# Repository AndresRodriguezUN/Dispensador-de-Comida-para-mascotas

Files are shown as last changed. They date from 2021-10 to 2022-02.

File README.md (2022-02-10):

# Dispensador de Comida para mascotas 🐱 🐶
## Autores :fountain_pen:
- Diego Steven Peña Cortes :mechanic:
- Daniel Machado Roa :technologist:
- Andrés Felipe Rodríguez Contreras :office_worker:  :shipit:

Este es el repositorio del proyecto final de la asignatura Sistemas Emebidos del semestre 2021-II (Universidad Nacional de Colombia - Sede Bogotá). A continuación se mostrará el proyecto de un Dispensador de Comida conformado por una arquitectura de SoC, donde a partir de un micropocesador y diferentes periféricos se realizan operaciones que permiten al dispensador vincularse con un dispositivo movil para configurar la alimentación de la mascota.
 
 ## Proyecto :open_file_folder:
 El proyecto consiste en un dispensador de comida para mascotas que dispone de funcionalidades como la comunicación con una app movil que permite la configuración del dispositivo y el funcionamiento del mismo. Dentro del funcionamiento se encuentra la programación de los horarios de alimentación, asi como la interacción entre el usuario-dispositivo-mascota.
 
Por otro lado, el dispositivo cuenta con sensores que permiten detectar si la mascota está comiendo, además de los horarios que frecuenta el dispositivo. Y de esta manera, puede realizar un análisis de los datos y retroalimentar al usuario por medio de la actualización de los comportamientos de su mascota frente al dispositivo. Permitiendo que no se pierda la conexión que tiene el usuario con su mascota.  
 
 ## [Motivación](/Motivacion/) :thought_balloon:
 
 Con el fin de de justificar el proyecto, se definieron los viajes tanto del cliente como de la mascota y del como intervenía nuestro proyecto en cada uno de los trayectos. Esto permitio resaltar las funcionalidades directas o indirectas que debe cumplir el dispositivo a desarrollar. De esta forma se definieron los periféricos necesarios, además del módulo-procesador que se van a utilizar.

 ## Flujo de procesos
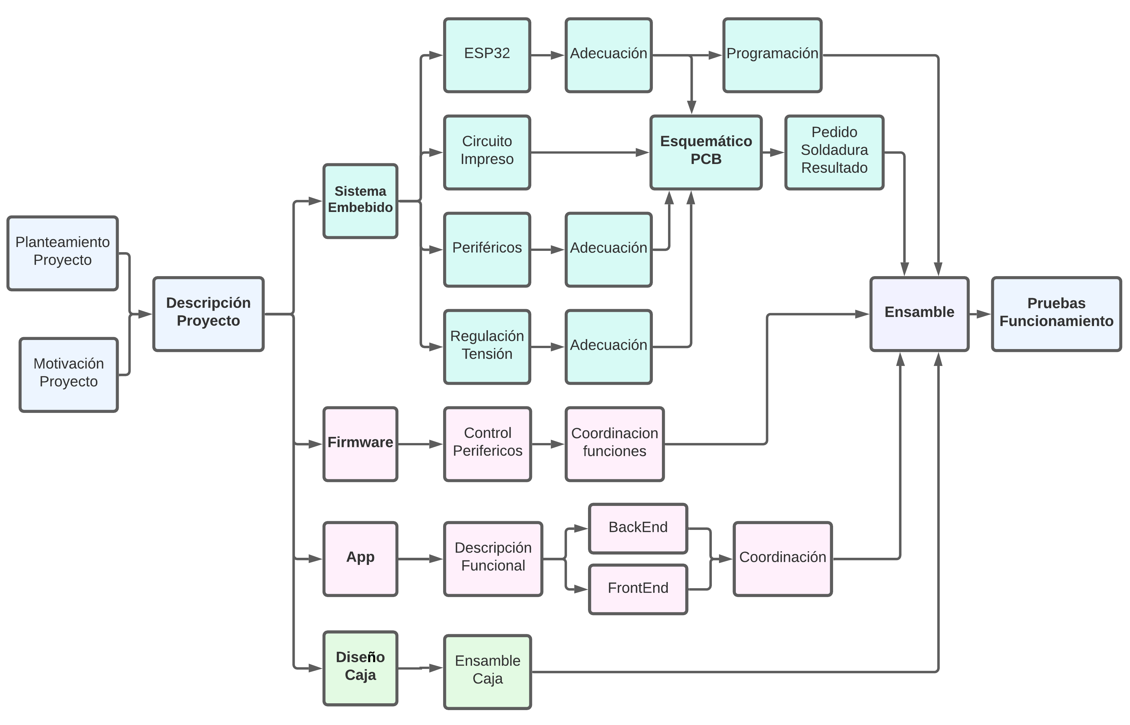
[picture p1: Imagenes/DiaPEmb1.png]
 

 ## [Sistema embebido](/SoC/)  :computer:
 
 El sistema embebido se definio gracias al análisis previo de las funcionalidades directas e indirectas del dispositivo, las cuales permitieron decidir los periféricos necesitados para cumplir cada una de las funcionalidades del proyecto.
 
### Periféricos

- [Pantalla OLED - I2C](/Perifericos/OLED)

- [Sensor de movimiento](/Perifericos/SensorMov)

- [Sensor infrarrojo](/Perifericos/SensorInfra)

- [Control motor - ULN2003](/Perifericos/Motor)

- [DFPlayer Mini](/Perifericos/DFPlayer)
 
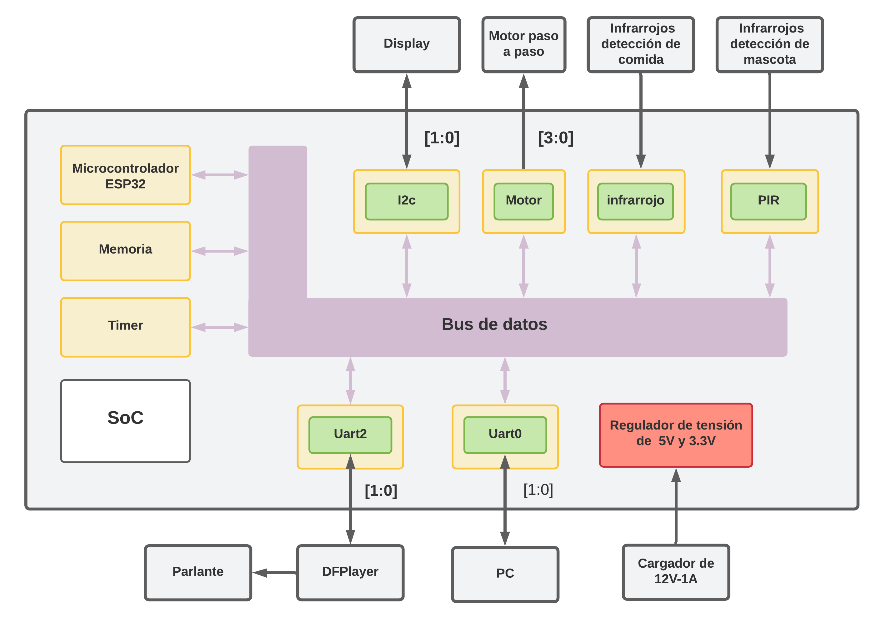
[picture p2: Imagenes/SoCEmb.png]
 
 
  ## Finalidad coordinación de periféricos :nut_and_bolt:
  
  La idea es construir un dispositvo que a determinadas horas del dia ponga a disposición una porcion de comida para nuestra mascota. Esta meta se cumple con las prestaciones que nos ofrece cada uno de los componentes a ensamblar:
  
  - Tarjeta basada en ESP32: Encargada de la coordinación de los périfericos y la comunicación inalámbrica con una App.
  - App: Encargada de la retroalimentación del usuario sobre el estado de la mascota, además de la posibilidad de programar los horarios de comida que el usuario desée para su mascota.
  - Motor: Encargado de la rotación del plato en el cual estan alojadas cada una de las porciones de comida.
  - OLED: Encargado de dar una retroalimentación visual, en el dispositivo, del estado de la mascota.
  - DFP y Parlante: Encargados de reproducir una pista de audio que avise a la mascota cuando llegue la hora de comer.
  - PIR: Encargado de detectar si la mascota se acerca al dispositivo dispensador de comida, para evaluar indirectamente su estado de ánimo.
  - Infrarrojo: Encargado de detectar si la mascota ha comido alguna parte de su ración, para evaluar indirectamente su estado de ánimo.
 
Al tener todo coordinado se espera que se cumpla la finalidad del proyecto satisfactoriamente.

## [Firmware](/Firmware) :man_technologist:
El firmware de todo el proyecto se desarrolla en micropython, el cual es una version renderizada de python para poder ejecutarse en microcontroladores como lo es el ESP32. Se decidio utilizar micropython debido a su practicidad y la documentación amplia que tiene en distintos repositorios. Con respecto al ESP32 cabe destacar que se debe flashear con micropython para que todos los códigos en python que se deseen emplear se ejecuten a la perfección. Para más información sobre el manejo de micropython junto al ESP32 por favor remitase a [micropython-esp32](https://docs.micropython.org/en/latest/esp32/tutorial/index.html).

## [App](/App) :calling:

Para poder manejar el dispensador de alimentos para mascotas se creó una aplicación, la cual permita modificar los valores de tiempo en que se servirán las comidas y a su vez saber el estado en que se encuentra la mascota.

## [Diseño Caja](/Rcaja) :triangular_ruler: :package:

Se diseñó un contenedor (carcasa o caja) la cual permitiera tener el dispensador dentro de una estructura con el fin de almacenar el plato con la comida y el sistema embebido, por lo tanto, se tomaron las diferentes medidas de los periféricos para poder crear los planos en *CorelDraw* y crear la carcasa en madera gracias al proceso de corte láser.

## [Ensamble](/Ensamble) :wrench:

En esta sección se muestra el paso a paso de la unión del sistema embebido y el plato que contiene la comida con la carcasa por medio de imágenes que dan evidencia de este proceso. 

## Pruebas de funcionamiento y videos de referencia :clapper:

### Videos de referencia
Para encontrar los videos que se recomiendan a lo largo del repositorio por favor dirijase a [videos proyectos pasados](https://www.youtube.com/channel/UCFcKXg10MjH98TOnZhloZSA).

### Pruebas de funcionamiento

Se realizaron las siguientes pruebas de funcionamiento del dispositivo y la App.

- [Prueba 1](https://youtu.be/kQyHtM4AsF8).
- [Prueba 2](https://youtu.be/hgBiyUTOZwg).

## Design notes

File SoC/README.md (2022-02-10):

# Sistema embebido :computer:

## [Microcontrolador ESP32](/SoC/ESP32/)
Se implementó un microcontrolador ESP32-WROOM, el cual se encargara de coordinar los diferentes periféricos a implementar. Igualmente, gracias a su periférico de WiFi se podrán utilizar las comunicaciones inalámbricas en lo que respecta a la conexión con la App de control.

- [Adecuación y acondicionamiento](/SoC/ESP32#adecuaci%C3%B3n)
- [Programación](/SoC/ESP32#programaci%C3%B3n)

## Periféricos

En base al sistema embebido definido previamente, se llegó a la conclusión que los periféricos necesarios para cumplir con las funcionalidades directas del dispositivo son:

- [Pantalla OLED - I2C](/Perifericos/OLED)

- [Sensor de movimiento](/Perifericos/SensorMov)

- [Sensor infrarrojo](/Perifericos/SensorInfra)

- [Control motor - ULN2003](/Perifericos/Motor)

- [DFPlayer Mini](/Perifericos/DFPlayer)

## [Regulación de tensión](/Regulador)

Dado que en proyecto se utiliza un ESP32-WROOM, este necesita una tensión de 3.3V para funcionar y por otro lado se necesitan 5V para poner en funcionamiento un motor paso a paso que se encargara de las prestaciones mecanicas del dispositivo. Por lo tanto se implementan dos reguladores de tension en la tarjeta que se desarrolle.

## [Circuito Impreso](/SoC/CircuitoImpreso)

Para el proyecto se decidio implementar un circuito impreso, el cual debera contar con el microcontrolador y los diferentes acondicionamientos necesarios para el manejo y control de los distintos periféricos a emplear.

- [Esquematico](/SoC/CircuitoImpreso#esquematico---kicad)
- [Asignacion de Footprints](/SoC/CircuitoImpreso#asignaci%C3%B3n-de-footprints)
- [PCB](https://github.com/AndresRodriguezUN/Dispensador-de-Comida-para-mascotas/tree/main/SoC/CircuitoImpreso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)
- [Pedido](/SoC/CircuitoImpreso#pedido---fabricante-chino)

## [Soldadura y Resultado](/SoC/Soldadura)

Con el circuito impreso entregado por el fabricante, se procede a realizar la soldadura de cada uno de los componentes comprados para el dispositivo dispensador de comida para mascotas.

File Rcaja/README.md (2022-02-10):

## Diseño de Caja :triangular_ruler::package:

Para realizar el diseño de la caja primero se debieron tener en cuenta el plato en donde se servirá la comida a la mascota, para esto se consiguió un plato de 21cm de diámetro con 8 cm de alto. A su vez, se deben tener en cuenta que para su creación se usó corte laser en madera, por lo tanto no se podría realizar una forma redonda a la carcasa, de esta manera se optó por formar un octágono que encierre el diámetro del plato sin problemas.

También cabe destacar que se debieron tener en cuenta los espacios de los periféricos dentro de la carcasa, como por ejemplo el motor, dando así que se agregaran 3 cm de alto a la carcasa (11cm). Así mismo,están diferentes periféricos que se les debe crear un espacio en las paredes de la carcasa para la interacción externa con estos, los objetos y sus medidas en la caja se presentan a continuación:

- OLED: 2.5cm x 1.5 cm
- Interuptor: 1.9cm x 1.2cm
- Conección alimentación: 9cm x 11cm
- Sensor PIR: 9mm diametro
- Conección USB: 1.5cm x 0.6 cm

Por lo tanto, teniendo en cuenta lo anterior se decidió realizar el proyecto el el programa de *CorelDraw* dando asi los siguientes planos:

<p align="center">
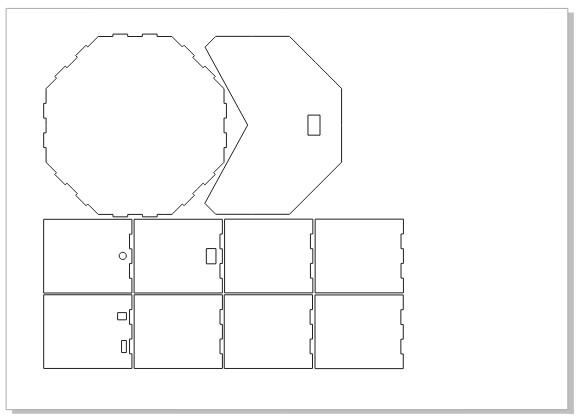
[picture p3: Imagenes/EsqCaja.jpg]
  

Por último, luego de mandar a cortar una tabla de madera en corte laser se obtuvo el siguiente resultado:

<p align="center">
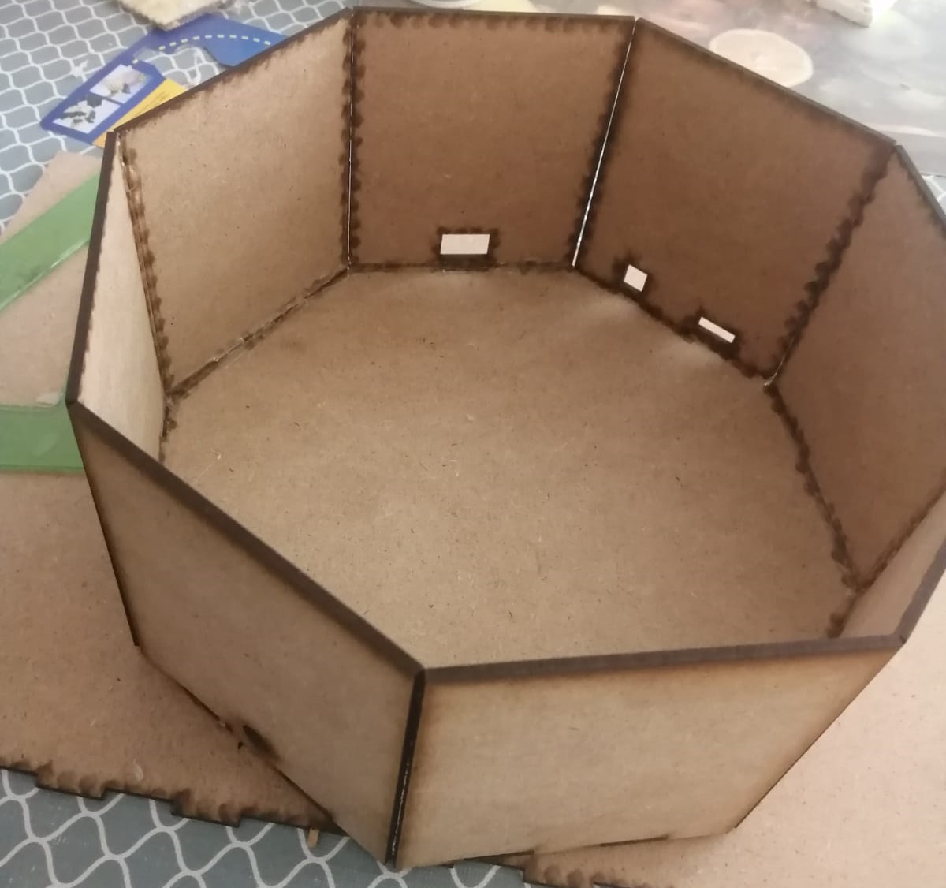
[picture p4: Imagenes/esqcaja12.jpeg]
  
</p>
<p align="center">
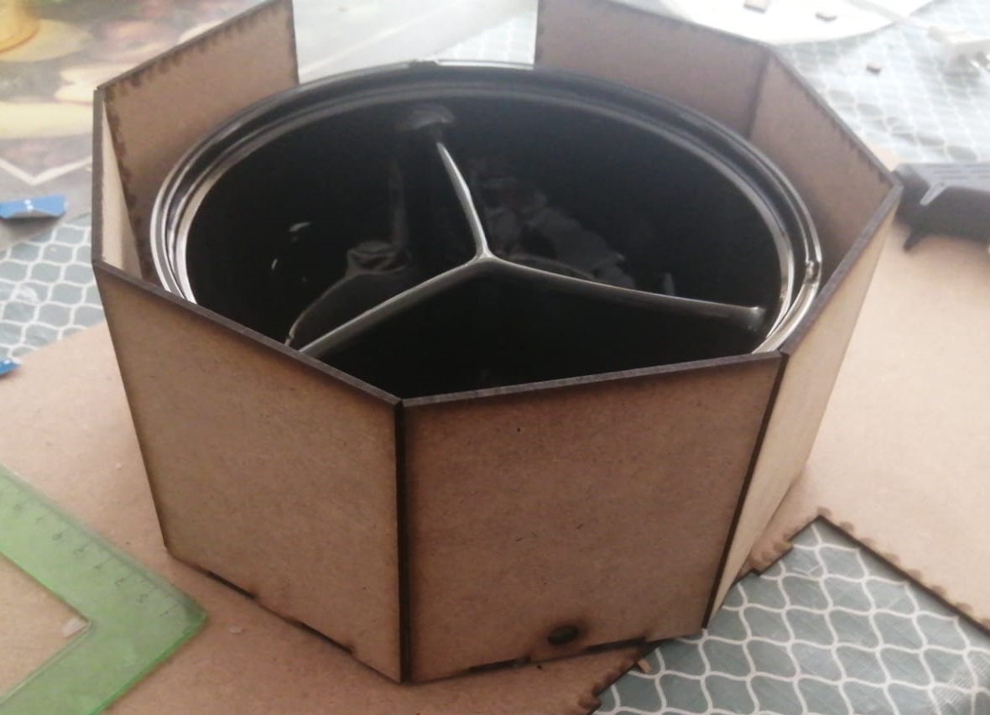
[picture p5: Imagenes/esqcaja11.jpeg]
  
</p>

Ya con la carcasa ensablada y las paredes pegadas, se puede pasar a colocar el circuito, los perifericos y el plato dentro para comenzar a hacer pruebas.

<p align="center">
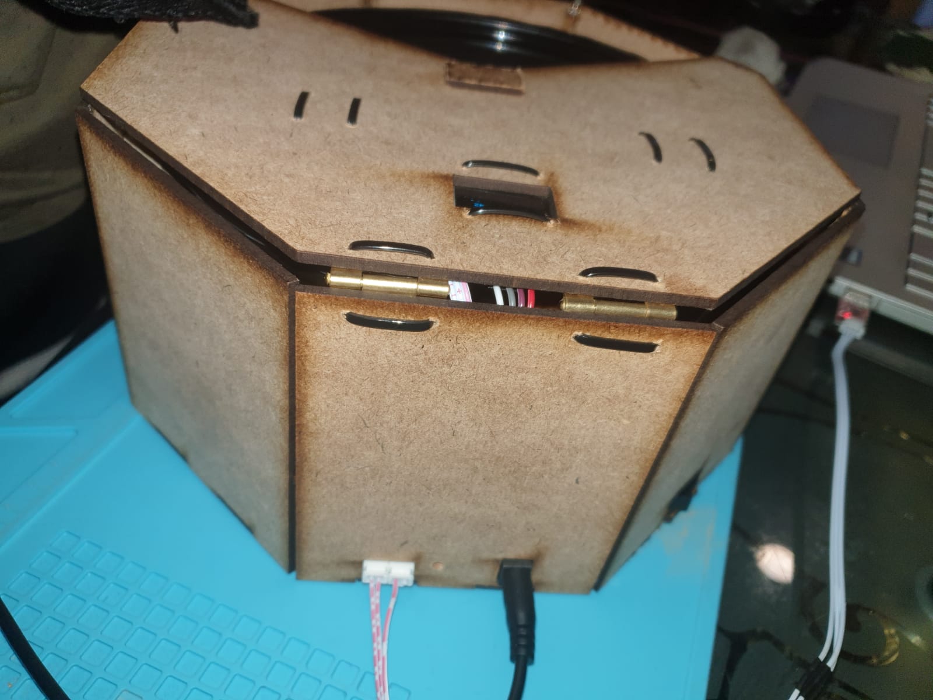
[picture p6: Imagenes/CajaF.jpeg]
  
</p>
<p align="center">
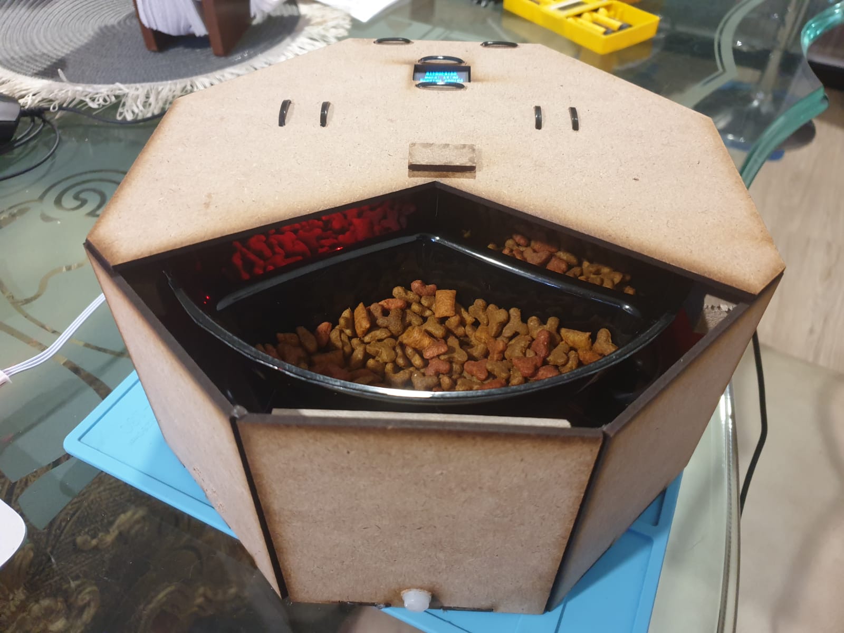
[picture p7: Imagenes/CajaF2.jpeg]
  
</p>

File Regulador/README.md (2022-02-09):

# Regulación de tension

El proyecto se utiliza un ESP32-WROOM, este necesita una tension de 3.3V para funcionar y por otro lado se necesitan 5V para poner en funcionamiento un motor paso a paso que se encargara de las prestaciones mecanicas del dispositivo. Por lo tanto se implementan dos reguladores de tension en la tarjeta que se desarrolle.
Con el fin de regular la tensión a 3.3 V y 5 V, se utilizan reguladores NCP1117-3.3 y NCP1117-5 con el empaquetado SOT-223.
<p align="center">
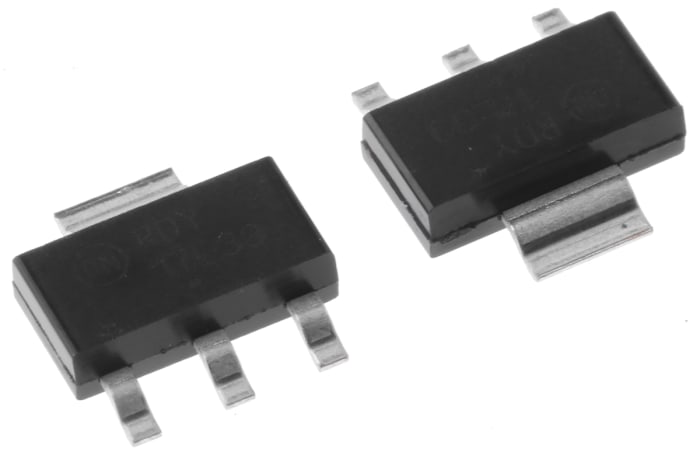
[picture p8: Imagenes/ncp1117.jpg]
  
</p>

## Diagrama de conexiones
Es importante identificar los pines de cada uno de los empaquetados para el correcto montaje sobre el circuito impreso, asi como el acondicionamiento que es necesario darles para su correcta implementacion.

<p align="center">
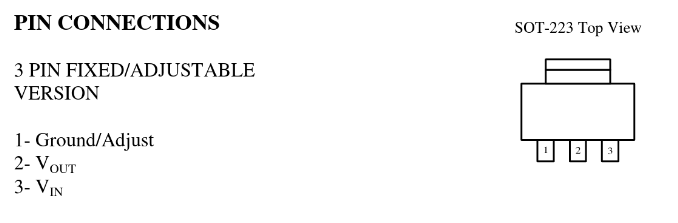
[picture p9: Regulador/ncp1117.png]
  
</p>

## Adecuacion
Segun el datasheet es necesario utilizar capacitores de 10uF y 47uF en la entrada y la salida correspondientemente, para cada una de las configuraciones de los reguladores de montaje SMD que se utilizaran en el circuito impreso. 

<p align="center">
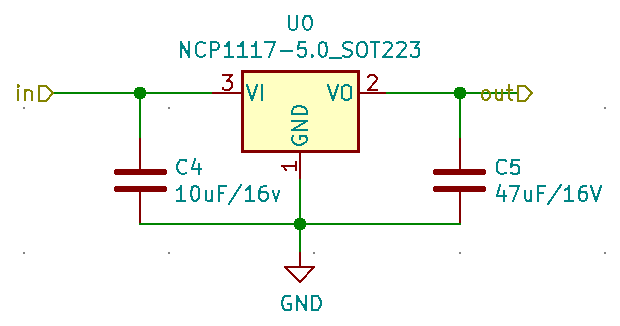
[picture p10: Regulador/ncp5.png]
  
</p>
<p align="center">
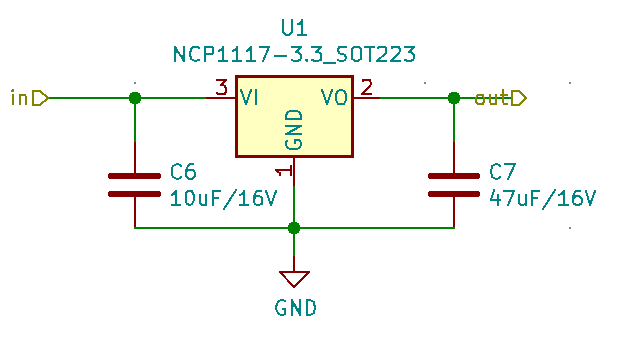
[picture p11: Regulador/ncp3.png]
  
</p>

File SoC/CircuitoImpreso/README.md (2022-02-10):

# Circuito Impreso
El circuito impreso se desarrolla teniendo en cuenta las adecuaciones y acondicionamientos que necesitan tanto el ESP32, los reguladores de tension y los perifericos. Para el desarrollo del esquematico y la PCB se utilizo el software de kiCAD, al cual fue necesario adicionarle las librerias correspondiente al esquematico del ESP32-WROOM y el footprint para la PCB.

## Esquematico - KiCAD
Despues de realizar el analisis de los distintos componentes y de los acondicionamientos necesarios, se realizo el esquematico en KiCAD de todo el proyecto. Incluyendo otras partes necesarias en hardware para la sujecion y conexion del sistema embebido. Igualmente dentro del repositorio se incluye el archivo del esquematico al cual puede remitirse para verificar todo lo diseñado [kiCAD](/kiCAD). 

### ESP32-WROOM
- Conexiones en general del microcontrolador.
<p align="center">
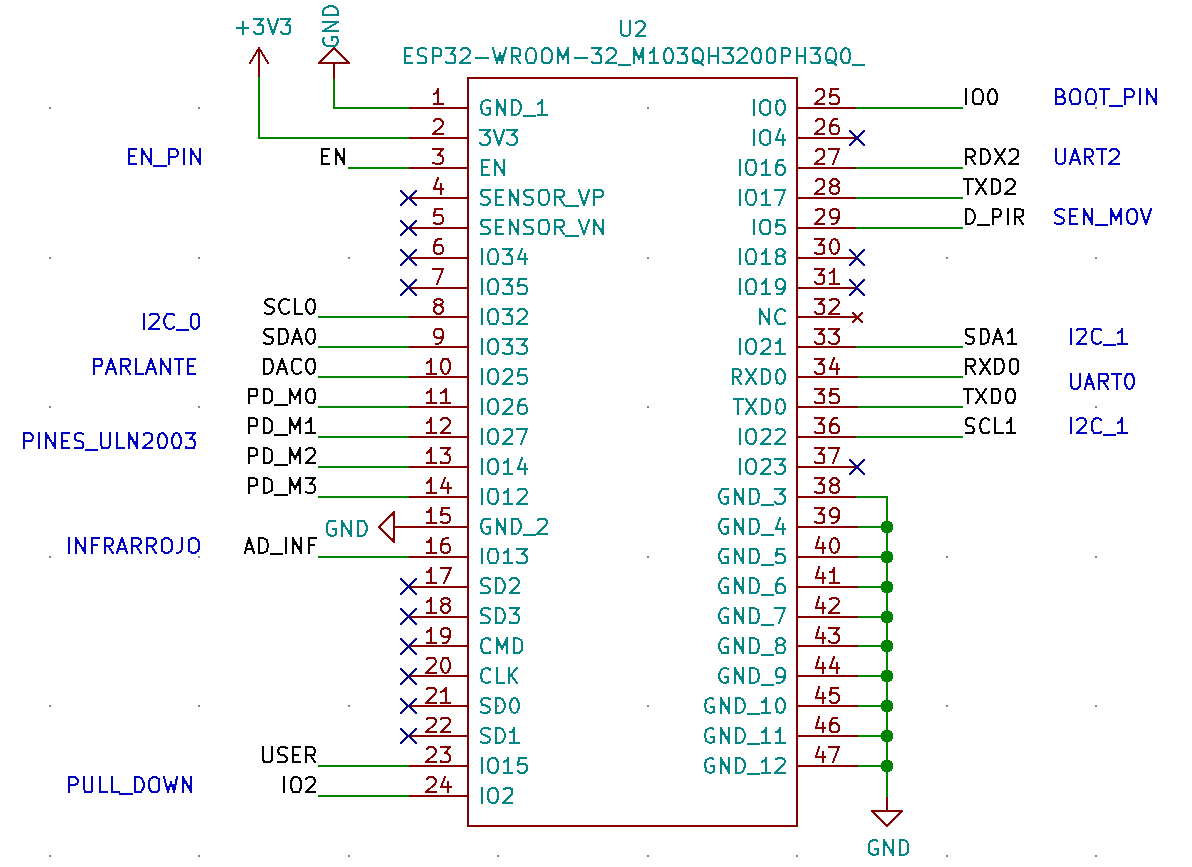
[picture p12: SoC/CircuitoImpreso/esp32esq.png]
  
</p>

- PIN USER: Este Pin se utiliza para interactuar visualmente con el ESP32 y verificar si funciona correctamente tanto la recepcion, como transmision de datos.

<p align="center">
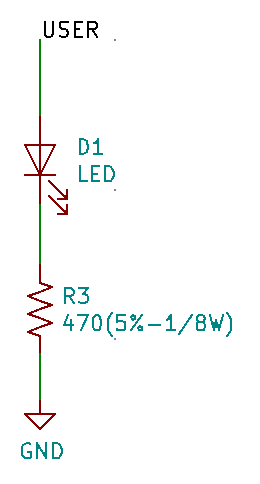
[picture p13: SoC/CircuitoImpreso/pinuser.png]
  
</p>

- PIN 2: Este Pin es importante que este en PULL-DOWN cuando el ESP32 se necesite que este en BOOT-MODE, por lo que se conecta una resistencia de 10kOhm para llevarlo a GND.

<p align="center">
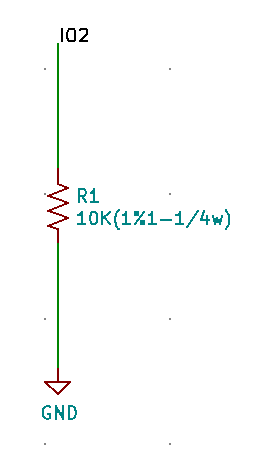
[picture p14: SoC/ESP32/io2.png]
  
</p>

- PIN 0: Este Pin es de booteo, por lo tanto de acuerdo a lo recopilado de distintos repositorios, se requiere implementar un boton que al ser presionado ponga al PIN 0 en PULL-DOWN.

<p align="center">
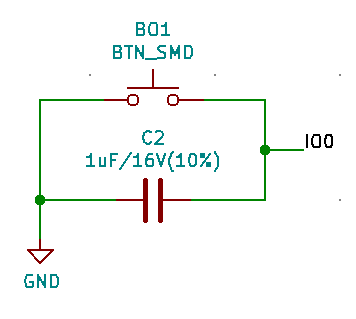
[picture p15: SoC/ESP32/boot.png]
  
</p>

- PIN EN: Este Pin es el ENABLE, y tiene que estar en PULL-UP todo el tiempo. Sin embargo para cuando sea necesario resetear el ESP32 tiene que estar en PULL-DOWN. Por lo tanto se implementa un boton que realiza la misma funcion que el de Booteo y tiene la siguiente arquitectura.

<p align="center">
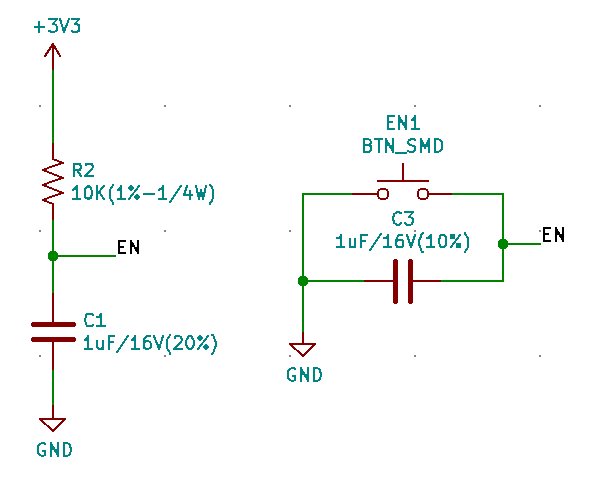
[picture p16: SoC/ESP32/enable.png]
  
</p>

- PIN 3V3: Se implementa un capacitor ByPass de 100pF para filtrar todo el ruido que pueda afectar la alimentacion del ESP32 (este capacitor se debe procurar que este lo suficientemente cerca de el pin 3V3).

<p align="center">
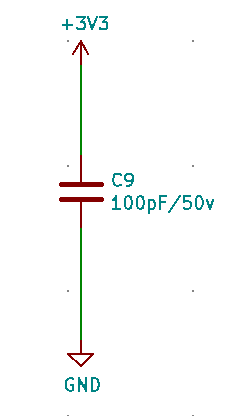
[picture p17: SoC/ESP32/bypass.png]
  
</p>

### Motor paso a paso
- Configuracion del ULN2003 y caja negra del driver del motor paso a paso.
<p align="center">
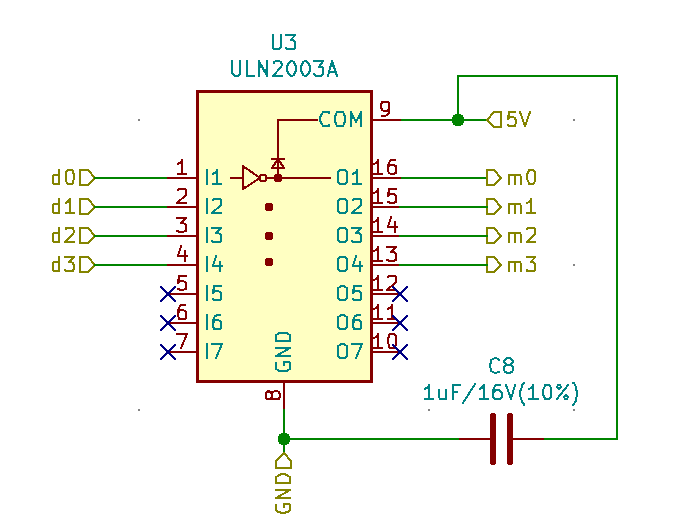
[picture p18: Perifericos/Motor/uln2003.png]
  
</p>
<p align="center">
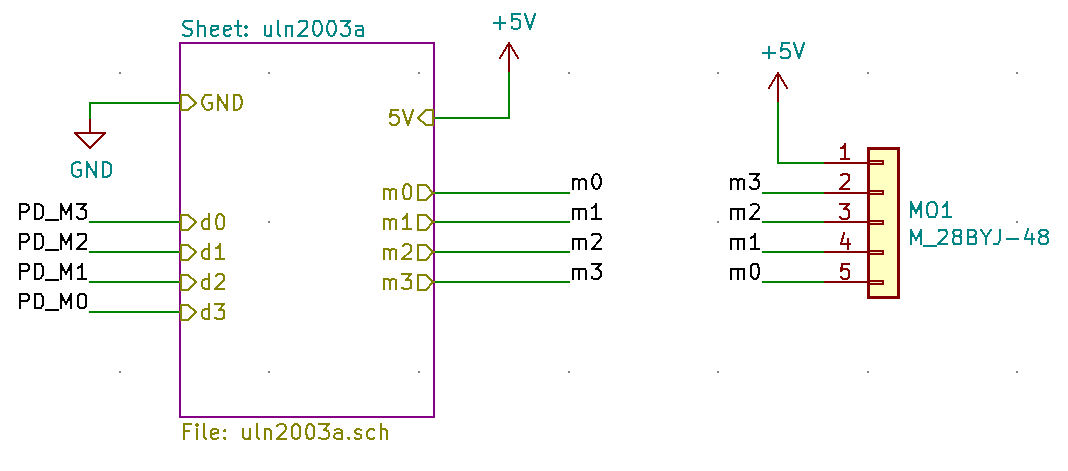
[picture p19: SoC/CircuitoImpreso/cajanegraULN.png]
  
</p>

### Regulacion y conexion Jack-DC

- Acondicionamiento de reguladores

<p align="center">
  
</p>
<p align="center">
  
</p>

- Conexion Jack-DC para cargador de 12V, en donde se deja una salida para conectar un interruptor que permita apagar y prender el dispositivo.

<p align="center">
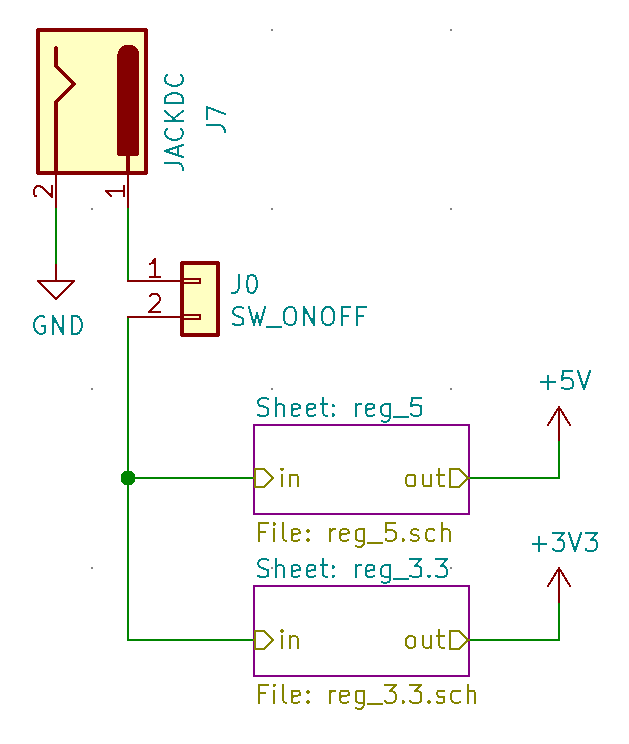
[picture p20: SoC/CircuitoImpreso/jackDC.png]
  
</p>

### Conectores para los perifericos en general
Se utilizaron conectores de diferente cantidad de pines para poder ajustar los pines para cada uno de los perifericos.

<p align="center">
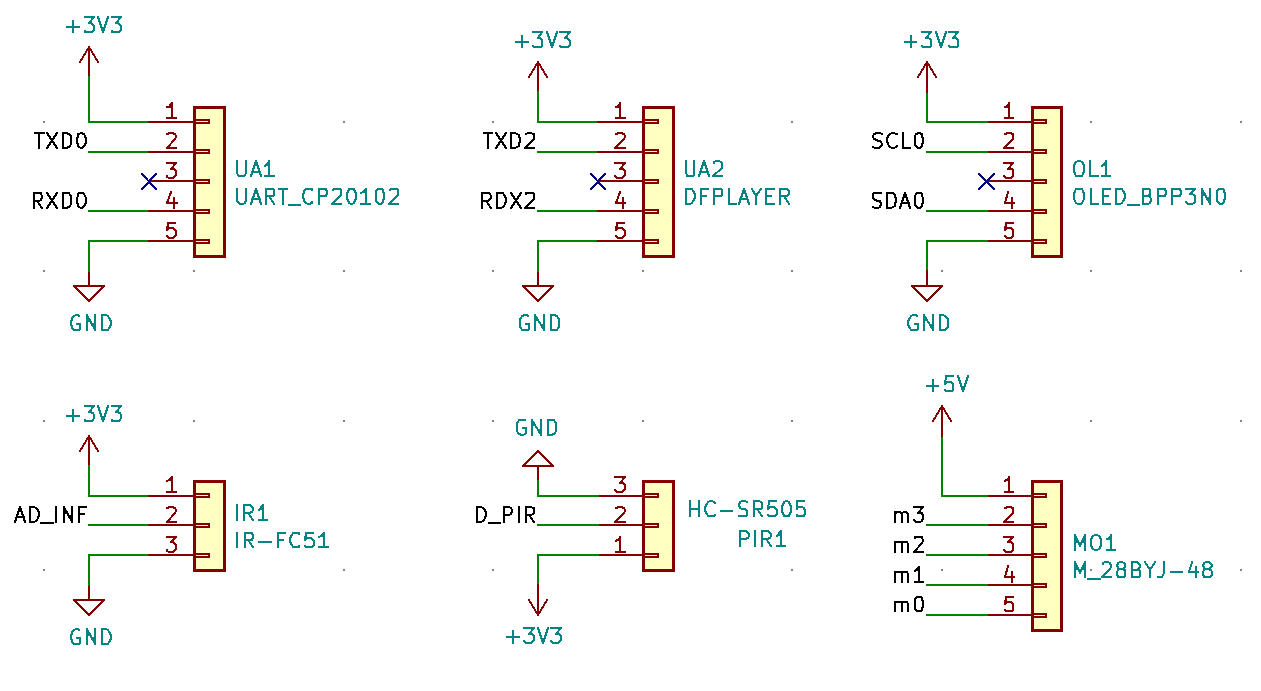
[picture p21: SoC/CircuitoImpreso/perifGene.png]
  
</p>

## Asignación de Footprints
Antes de continuar con la generacion de la PCB y la NetList, se asignan las footprint para cada uno de los elementos que se implementaron en el montaje del circuito impreso. En este paso se debe tener en cuenta los componentes que se van a comprar y las dimensiones, para que de esta forma se puedan realizar una correcta seleccion de cada uno de los footprints asociados (y que no vayan a haber problemas a futuro por una mal encuadre de dimensiones).

<p align="center">
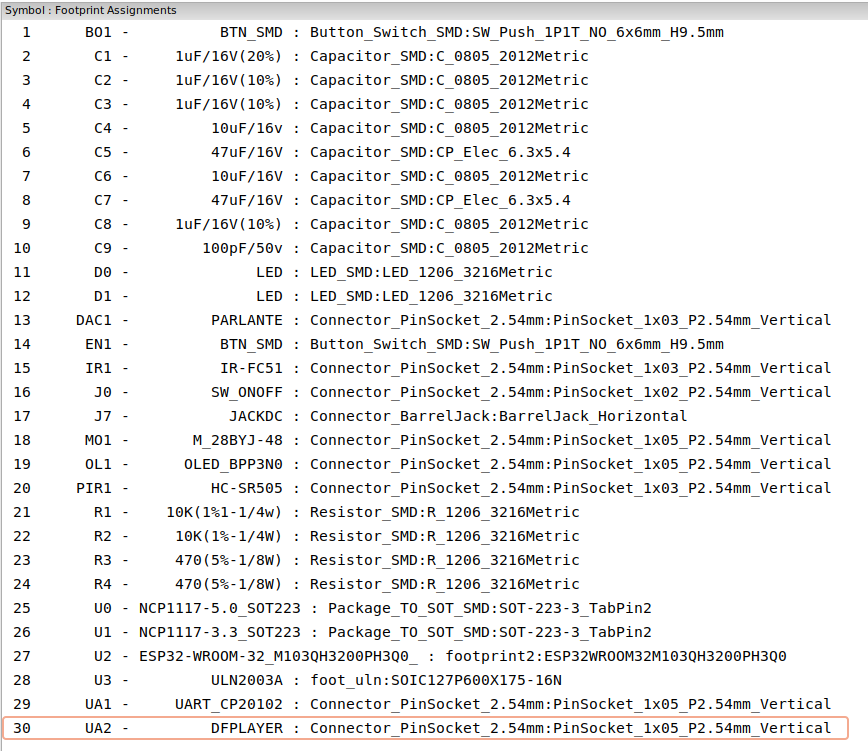
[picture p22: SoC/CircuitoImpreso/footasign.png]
  
</p>

## PCB - KiCAD

Despues de realizar el diseño en kiCAD del esquematico, se procede a generar la PCB junto con las footprints asociadas previamente. En donde se cuadra la ubicacion de todos los componentes en el circuito impreso teniendo en cuenta una distribucion por potencia (separando por secciones imaginarias los componentes de mayor a menor potencia), asi como las recomendaciones de dimensiones minimas que podia implementar el fabricante. Del mismo modo se incluyen otras partes necesarias en hardware para la sujecion del sistema embebido. Igualmente dentro del repositorio se incluye el archivo de la PCB al cual puede remitirse para verificar todo lo diseñado [kiCAD](/kiCAD). 

<p align="center">
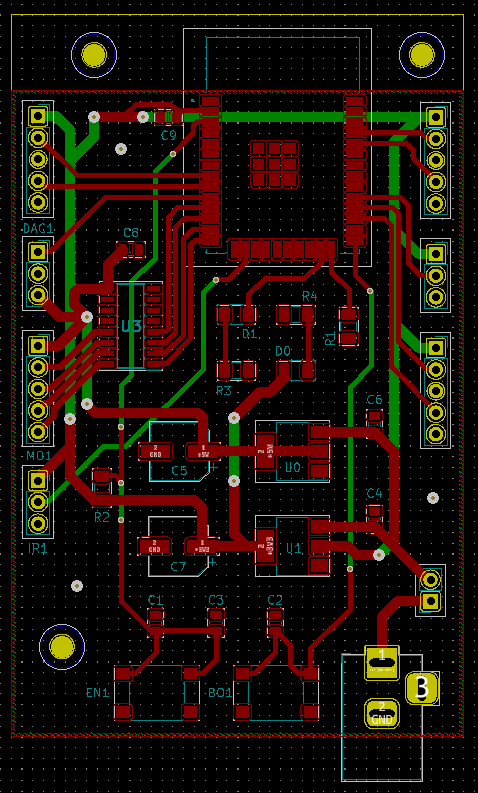
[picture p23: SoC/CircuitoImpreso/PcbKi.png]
  
</p>

Como se puede observar, se adicionaron o ajustaron ciertas cosas adicionales en la PCB como lo son:

- Orificios de sujecion, por lo cuales seria ideal ajustar la placa en el dispositivo.
- Segun la guia de diseño, es importante que para el correcto funcionamiento de la antena de el ESP32, se debe despejar el area de cualquier pista de cobre que pase por la seccion de la antena.
<p align="center">
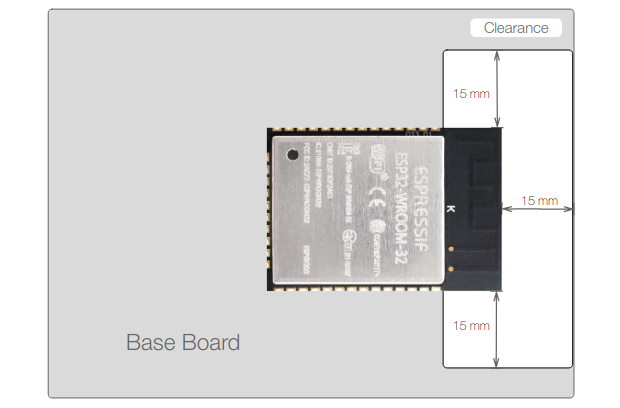
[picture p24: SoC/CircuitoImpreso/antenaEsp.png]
  
</p>

- Se implementaron **vias** en las zonas donde no habian componentes, para reducir la capacitancia entre las caras asignadas a tierra del circuito impreso. 

## Pedido - fabricante CHINO

El pedido se realizo a un fabricante chino, especificamente a [JLCPCB](https://jlcpcb.com/), y el proceso que se realizo en resumidas cuentas es el siguiente:

- Subir el archivo del proyecto, no sin antes generar los archivos gerber y de perforacion del proyecto. Y en la pagina del fabricante se detallan las caracteristicas que el usuario prefiera para la fabricacion de su PCB.

<p align="center">
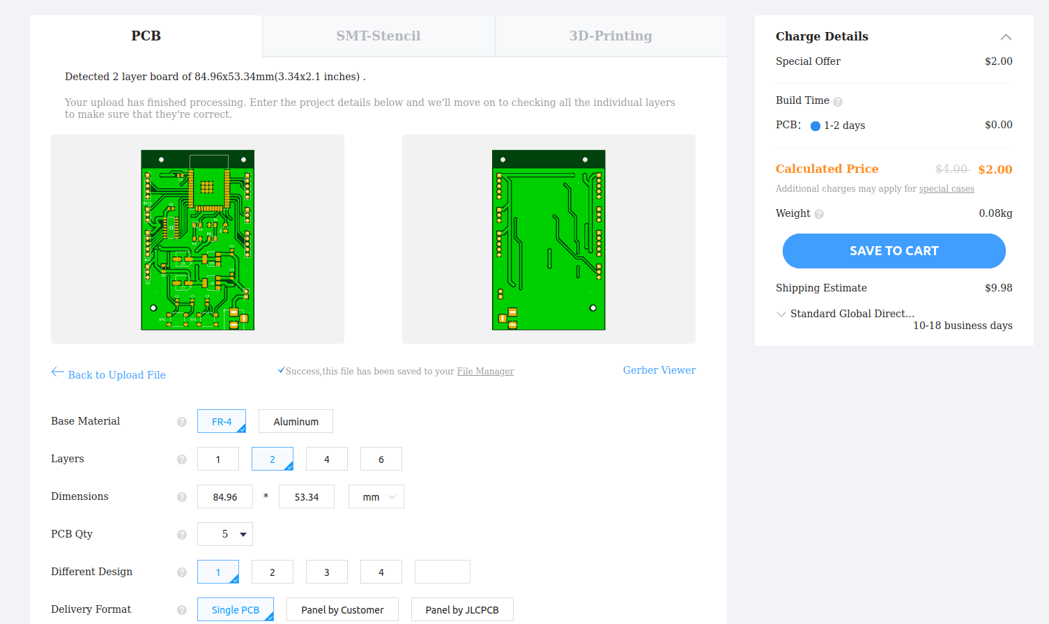
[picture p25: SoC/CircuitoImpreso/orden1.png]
  
</p>

- Posteriormente que se llene la informacion de las caracteristicas de la placa, se procede al carrito de compras y se verifica el precio estimado por la fabricacion de la cantidad que se halla exigido (la minima cantidad que se fabrica son 5 placas por $2 Dolares).

<p align="center">
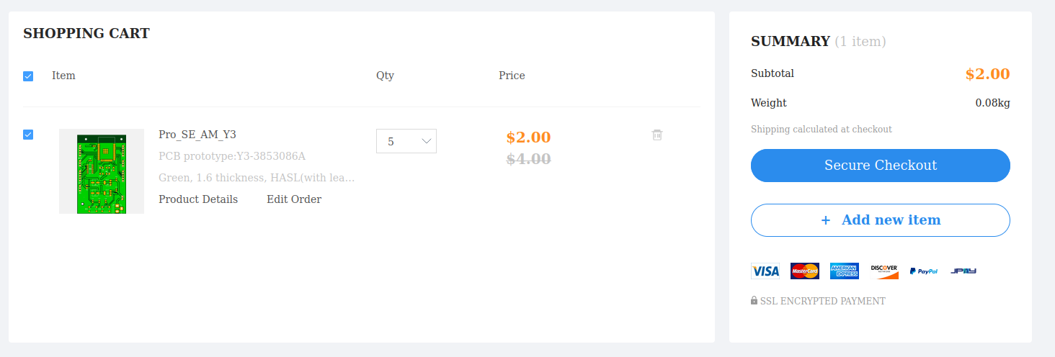
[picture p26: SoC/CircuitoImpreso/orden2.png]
  
</p>

- Luego se procede con el diligenciamiento de la informacion respectiva a la residencia y de facturacion, para continuar con el metodo de envio. **El metodo de envio que recomendamos y que nos funciono a nosotros es el Standard Special Air Mail**. Ya que es el unico que hace envios a Colombia, por un precio razonable en un plazo de alrededor de 20 dias.

<p align="center">
  
</p>

- Y luego de 20 dias asi llego la PCB.

<p align="center">
  
</p>

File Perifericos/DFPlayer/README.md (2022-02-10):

# DFPlayer Mini - Reproductor audio
La comunicación con el DFP player se basá que por el pin de TX (escritura) se envía una serie de 10 bytes las cuales estan organizados de la siguiente manera (para más informacion remitase a [DFPlayer](/Datasheets/DFP.pdf)):

| Byte | Descripción |
| --- | --- |
|  $$ | Para comenzar la comunicación y que el DFP player sepa que se estan comnicando con él |
| VER | La version (siempre la manejamos como FF) |
| Len | numero de bytes luego de esta posición |
| CMD | Comando que le quiere enviar al DPF player  |
| Feedback | Si se quiere saber retroalimentación del proceso que este haciendo |
| parm1 | Parametro 1 para dar una orden  |
| parm2 | Parametro 2 para dar una orden  |
| checksum | Suma y verificación de los valores que se van a enviar |
| $O | Byte final que dice que se termino la orden enviada |

De esta manera,para usar y dar ordenes al DFP player se usó una función llamada **sendInfo()** con la cual solo modificamos los valores de **CMD**, **parm1** y **parm2** para reproducir un audio, parar el audio, subir el volumen y demás. 

<p align="center">
  
</p>

Pasando a las conexiones del DFP player se usó el pin VCC para la alimentación de 5v, los pines RX y TX como se mencionó anteriormente irían conectados al ESP32 para la comunicación con la Uart y el manejo del periférico, el pin GND como la tierra y por ultimo el DFP player posee un espacio para almacenar una memoria SD la cual posee los audios utilizados en el proyecto. Estos audios son nombrados como 0001, 0002... Esto dado que al ingresar el **parm2** dentro de la orden del DFP player pueda encontrar y reproducir el audio.

## Adecuacion

Como se indicó previamente el DFPlayer mini se comunica con el microcontrolador por medio de UART, por lo que se reserva la UART2 exclusivamente para la comunicación con el DFP. Y no es necesario realizar más adecuaciones o acondicionamientos para el DFPlayer, más allá de los pines de alimentación y tierra que necesita.

- 2 pines UART2.
- 1 pin Vcc de 3V3.
- 1 pin de GND.

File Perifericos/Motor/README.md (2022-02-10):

# Motor
## Componentes
Los componentes que se van a utilizar para este periférico serán:

- Motor unipolar 28BYJ-48
- Driver ULN2003A

<p align="center">
  
</p>

## Estructura y funcionamiento
El funcionamiento del motor paso a paso 28BYJ-48 se basa en la activación de las distintas bobinas que tiene interiormente por medio de señales digitales. Para ajustar magneticamente la posición angular del rotor. Sin embargo esto no se puede realizar simplemente con las salidas digitales del ESP32 ya que no poseen la suficiente corriente para alimentar el motor paso a paso, por lo tanto se implementa el driver ULN2003 que es un arreglo de transistores en configuracion darlington que permiten una salida de corriente de hasta 500mA. PAra mas informacion remitase a nuestro video de youtube [Motor paso a paso - FPGA](https://www.youtube.com/watch?v=wyz6QGYnmfk).

<p align="center">
  
</p>

## Diagrama de conexiones
La idea es que las salidas digitales que se obtienen del ESP32 con las que se desea controlar el motor vayan primero al driver ULN2003 para que sea posible controlar el motor con la corriente necesaria. Por lo tanto se sigue el diagrama que está a continuación, para poderlo replicar en la tarjeta que se elaboara en la sección de circuito impreso.

<p align="center">
  
</p>

## Adecuación
La adecuación que necesita el circuito impreso es tener implementado un driver ULN2003, el cual se seleccionó para este caso de montaje superficial, pero además de eso es necesario utilizar un capacitor de Bypass a la entrada de tensión de 5V del driver para filtrar cualquier ruido que pueda interferir en el diseño. Por lo tanto se define lo siguiente:

<p align="center">
  
</p>

- 4 pines digitales.
- 1 pin Vcc de 5V exclusivo para el ULN2003.
- 1 pin de GND.

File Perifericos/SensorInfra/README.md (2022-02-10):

# Sensor infrarrojo

## Componentes

Los componentes que se van a utilizar para este periferico seran:

- Módulo Sensor Infrarrojo FC-51.

<p align="center">
  
</p>

## Estructura y funcionamiento

El sensor infrarrojo es un dispositivo optoelectrónico capaz de medir la radiación electromagnética infrarroja de los cuerpos en su campo de visión. Todos los cuerpos emiten una cierta cantidad de radiación, esta resulta invisible para nuestros ojos pero no para estos aparatos electrónicos, ya que se encuentran en el rango del espectro justo por debajo de la luz visible. 

<p align="center">
  
</p>

## Diagrama de conexiones
El sensor infrarrojo se puede utilizar como un medidor de distancia o un detector de obstaculos, por lo que presta dos salidas, una salida analógica y otra digital. Para el fin de nuestro proyecto se utilziara la salida digital para detectar si hay comida o no en el recipiente. De modo que solo se utilizara el pin digital y el analógico se dejará sin conexión alguna.

<p align="center">
  
</p>

## Adecuación

La comunicación con el infrarrojo es por medio de un pin digital. Por lo tanto lo unico que se necesita es prestar para el infrarrojo 3 pines:

- 1 pin digital de recepcion de datos.
- 1 pin de Vcc de 3V3.
- 1 pin de GND.

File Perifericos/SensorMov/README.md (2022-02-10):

# Sensor Movimiento

## Componentes
Los componentes que se van a utilizar para este periférico serán:

- Módulo Sensor Infrarrojo Piroeléctrico Mini HC-SR505.

<p align="center">
  
</p>

## Estructura y funcionamiento

El sensor PIR es un sensor electrónico que mide la luz infrarroja (IR) radiada de los objetos situados en su campo de visión. Lo que le permite detectar el movimiento y es util para las funcionalidades que se requieren para el dispositivo.

<p align="center">
  
</p>

## Diagrama de conexiones

El sensor PIR tiene una salida digital que indica si ha detectado o no movimiento, por lo tanto es necesario recibirla en el ESP32 para realizar el tratamiento de la información.

<p align="center">
  
</p>

## Adecuación
La comunicación con el PIR es por medio de un pin digital. Por lo tanto lo unico que se necesita es prestar para el PIR 3 pines:
- 1 pin digital de recepcion de datos.
- 1 pin de Vcc de 3V3.
- 1 pin de GND.

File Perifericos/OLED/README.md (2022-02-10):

# OLED
## Componentes
Para el proyecto se usara un OLed de referencia **OLED-128O064D-BPP3N00000**.

<p align="center">
  
</p>

## Estructura y funcionamiento 
La pantalla Oled funciona a partir de una alimentación de 3V (maximo 3.3V y minimo 2.8V) a su vez se logra trabajar con este componente gracias a la comunicación I2C, de esta manera como se logra ver en el siguiente apartado, el Oled posée dos pines para la comunicación que son SCL y SDA los cuales nos permiten la comunicación y trabajan de la siguiente forma (despues se describe con más detalle).
## Diagrama de conexiones
Por último, dado que se usara la comunicación I2C solo sera necesario usar 4 pines para la conexión del componente, VCC siendo la alimentación de 3V, GND el ground, SDL y SDA.

<p align="center">
  
</p>

## Adecuación

La comunicación con el OLED es por medio de i2c, y el periférico de i2c ya viene acondicionado en el SoC que el fabricante ofrece para el ESP32. Por lo tanto, lo unico que se necesita es prestar para el OLED 4 pines:
- 2 pines de i2c
- 1 pin de Vcc a 3V3
- 1 pin de GND

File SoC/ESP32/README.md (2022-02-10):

# Microcontrolador ESP32-WROOM

El microcontrolador ESP32 es un SoC basado en un procesador Xtensa LX6, el cual gracias a su hardware presta la funcionalidad de comunicacion inalámbrica gracias a su módulo de WiFi y Bluetooth. Por lo tanto se decidio utilizar especificamente la version ESP32-WROOM del mismo ya que se acomodaba justamente a las necesidades de hardware que se requerian para el funcionamiento del dispositivo dispensador de comida para mascotas.

<p align="center">
  
</p>

El ESP32-WROOM32 cuenta con 38 pines de los cuales se emplearan UART's, pines digitales y analogicos. Para mas informacion sobre la descripcion de los pines remitirse a [esp32wroom](/Datasheets/esp32-wroom-32_datasheet_en.pdf).

## Adecuación

Si bien el SoC del ESP32-WROOM viene con la adecuación de sus periféricos internos y los módulos que implementa para funcionar. Es necesario realizar la adecuación de este por medio de una serie de resistencias y capacitores para poderlo trabajar correctamente en la práctica. Muchos de los acondicionamientos que se van a listar aqui pueden funcionar para cualquier ESP32, sin embargo cabe resaltar que se realizan para el ESP32-WROOM (para más información puede tomar de guía [esp32wroom](/Datasheets/esp32-wroom-32_datasheet_en.pdf)).

- PIN 2: Este Pin es importante que este en PULL-DOWN cuando el ESP32 se necesite que este en BOOT-MODE, por lo que se conecta una resistencia de 10kOhm para llevarlo a GND.

<p align="center">
  
</p>

- PIN 0: Este Pin es de booteo, por lo tanto de acuerdo a lo recopilado de distintos repositorios, se requiere implementar un botón que al ser presionado ponga al PIN 0 en PULL-DOWN.

<p align="center">
  
</p>

- PIN EN: Este Pin es el ENABLE, y tiene que estar en PULL-UP todo el tiempo. Sin embargo para cuando sea necesario resetear el ESP32 tiene que estar en PULL-DOWN. Por lo tanto se implementa un botón que realiza la misma función que el de Booteo y tiene la siguiente arquitectura.

<p align="center">
  
</p>

- PIN 3V3: Se implementa un capacitor ByPass de 100pF para filtrar todo el ruido que pueda afectar la alimentación del ESP32 (este capacitor se debe procurar que esté lo suficientemente cerca de el pin 3V3).

<p align="center">
  
</p>

## Programación

La programación del ESP32 se realizara por medio de el periférico UART0 que ya presta el SoC. Sin embargo es necesario utilziar un conversor USB-UART para poder cumplir con el fin de comunicación entre el PC y el ESP32. 

<p align="center">
  
</p>

Y para el manejo del Firmware que se utilizara para coordinar los diferentes periféricos y el ESP32 se decidio utilizar MicroPython debido a su simplicidad y la amplia gama de información que se puede encontrar en repositorios para alguna funcionalidad en especifico que esa necesaria utilizar. Para más información remitase a [Firmware](/Firmware). 

<p align="center">
  
</p>

Según lo que indica el datasheet, la coordinación de los pines IO0 y EN para ponerlo en BOOT-MODE debe ser la siguiente, a partir de la distribución de botones que se utilizó:
- Se deben presionar los dos botones BO y EN a la vez y se deben mantener presionados.
- Luego hay que dejar de presionar el EN, y mantener presionado el BO.
- Cuando se verifique que el firmware se este subiendo, o que se ha generado una buena conexion entre el PC y el ESP32 se puede dejar de presionar el BO.

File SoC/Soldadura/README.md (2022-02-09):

# Soldadura y Resultado

## Soldadura

Con respecto a la soldadura se procuro utilizar un cautin con un punta bastante fina para soldar el ESP32 como los componentes pequeños como lo son los capacitores y resistencias, asi como los componentes discretos correspondientes al ULN2003 y los reguladores de tension.

- Se recomienda utilizar flux para la soldadura del ESP32, ya que permite que el estaño aplicado se distribuya sobre los pads correctamente.
- Soldar los componentes en orden dependiendo de su altura, se recomienda soldar en primer lugar los componentes con la menor altura para que luego al soldar el resto no hayan complicaciones debido a la obstruccion. Y que se pueda utilizar el cautin con toda la libertad posible.
- Para la soldadura de los pines y el jackDC se recomienda utilizar una punta de cautin de un diametros mayor para que el estaño no se quede sujeto a la punta del cautin y se pueda adherir a los pines que se estan soldando.
- Para la soldadura en general se utilizo una estacion de soldadura, y la temperatura a la cual se trabajo fue de 350C (grados centigrados).

## Resultado

Despues de haber realizado la soldadura, el resultado de la tarjeta de desarrollo es el siguiente:

<p align="center">
  
</p>

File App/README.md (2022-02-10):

# APP :calling:
Se diseñó una aplicación móvil por medio de la plataforma APPInventor, la cual permite al usuario programar el número de comidas por día y el horario correspondiente. De igual forma el usuario, haciendo uso de la aplicación, podrá observar el estado de la mascota junto a la hora y el tiempo restante para la próxima comida.

## Viaje del usuario en la APP

### Screen de Carga

Al momento de iniciar la aplicación, el usuario observa en primer lugar la screen de carga. 

<p align="center">
  
</p>

### Registro

La primera vez que el usuario ingresa a la app, deberá completar los datos requeridos para personalizarla especificando el tipo de mascota, su nombre, el número de comidas y  horario correspondiente; esto por medio de la screen de registro. 

<p align="center">
  
</p>

### Menú principial 

En esta screen el usuario tendrá conocimiento del apetito de la mascota, además del tiempo restante para la próxima comida. De igual forma, por medio de esta screen el usuario podrá acceder a la screen de configuraciones y a la screen de información.

<p align="center">
  
</p>

### Configuraciones

La aplicación le permitirá al usuario modificar los datos de personalización ingresados inicialmente en la screen de registro.

<p align="center">
  
</p>

### Información 

En esta screen se indíca la información de los desarroladores de la aplicación y en general del dispensador de comida. 

<p align="center">
  
</p>

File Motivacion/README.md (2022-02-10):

# Motivación del proyecto :thought_balloon:

En principio el proyecto es una actualización-rediseño de un dispensador de comida realizado anteriormente  ([Dispensador mascotas 1.0](https://www.youtube.com/watch?v=MhDyZ9MV1TI)). Y como consecuencia se decide realizar un sistema embebido para cumplir con el objetivo del proyecto. Para realizar el análisis de la utilidad del proyecto se decide realizar el viaje del cliente tanto del usuario como de la mascota.
 ## Viaje del cliente

 ## Viaje de la mascosta


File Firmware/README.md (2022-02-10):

# Firmware :man_technologist:
El firmware de todo el proyecto se desarrolla en micropython, el cual es una version renderizada de python para poder ejecutarse en microcontroladores como lo es el ESP32. Se decidio utilizar micropython debido a su practicidad y la documentacion amplia que tiene en distintos repositorios. Con respecto al ESP32 cabe destacar que se debe flashear con micropython para que todos los códigos en python que se deseen emplear se ejecuten a la perfección. Adicionalmente, cabe aclarar que el archivo nombrado como **main.py** será el que se ejecute siempre que se reinicia el microcontrolador.

## Funcionalidad deseada

- Motor: Encargado de la rotación del plato en el cual estan alojadas cada una de las porciones de comida.
- OLED: Encargado de dar una retroalimentación visual, en el dispositivo, del estado de la mascota.
- DFP y Parlante: Encargados de reproducir una pista de audio que avise a la mascota cuando llegue la hora de comer.
- PIR: Encargado de detectar si la mascota se acerca al dispositivo dispensador de comida, para evaluar indirectamente su estado de ánimo.
- Infrarrojo: Encargado de detectar si la mascota ha comido alguna parte de su ración, para evaluar indirectamente su estado de ánimo.

## [main.py](/Firmware/main.py)

En primer lugar se adjuntan las librerias necesarias para el desarrollo del programa, asi como los modulos creados externamente que permiten reducir la cantidad de codigo gracias a la dinamica de programacion orientada a objetos.

<p align="center">
  
</p>

Se plantean todas las variables globales que se utilizaran en el codigo para poder editarlas en cada una de las funciones y se puedan utilizar en todo el desarrollo del codigo.

<p align="center">
  
</p>

En esta seccion se configuran los distintos perifericos de acuerdo a la necesidad que dictaban las correspondientes adecuaciones ya mencionadas.

<p align="center">
  
</p>

Dado que se utilizo un Broker Mosquito para la comunicacion con la aplicacion, es necesario plantear la logica de recepcion de datos.

<p align="center">
  
</p>

Asi mismo es importante establecer la conexion con el Broker MQTT, planteando un usuario y unos topicos de recepcion como de transmision de datos.

<p align="center">
  
</p>

Este bloque de codigo permite extraer el reloj UTC de la web, y luego se acondiciona con condicionales para ajustarlo a la zona horaria en la cual estamos ubicados.

<p align="center">
  
</p>

Y la ultima funcion empleada es la de coordinacion de las horas de alimentacion, asi como la cantidad de raciones al dia que se le sirven a la mascota.

<p align="center">
  
</p>

Para mas informacion sobre los codigos remitase a [main.py](/Firmware/main.py)

## [wlan.py](/Firmware/wlan.py)

El modulo wlan.py importa las librerias pertienentes para establecer la conexion WiFi, por medio de la clave y la contraseña del proveedor del usuario.

## [OLED.py](/Firmware/OLED.py)

El modulo OLED.py se ajusta de acuerdo al tamaño del OLED que se esta implementando, asi como un buffer que permite imprimir todo en el OLED al mismo tiempo.

## [DFP.py](/Firmware/DFP.py)

El modulo DFP.py se transcribio desde una referencia de un proyecto anteriormente realizado por el grupo. Y se adecuo al entorno de python para que funcionara el envio de datos al DFPlayer Mini.

## [motor.py](/Firmware/motor.py)

El modulo motor.py coordina la activacion de las bobinas del motor paso a paso, segun lo indicado en los videos de referencia del proyecto.

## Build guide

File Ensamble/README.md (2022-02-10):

# Ensamble :wrench:

## Ensamble - Tarjeta, Perifericos y Caja

El ensamble de todas las partes del dispositivo se realizó de la siguiente manera:

- En primer lugar, después de juntar y pegar cada una de las piezas de madera de la caja, se emplearon dos visagras para que la tapa superior de la caja fungiera como puerta, lo que permitiera acceder a cada uno de los compartimientos cuando se necesitara suplir con comida el dispensador.

<p align="center">
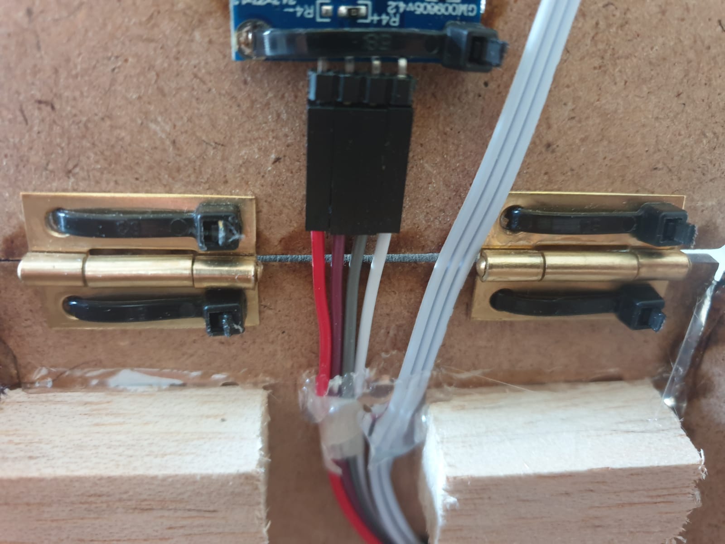
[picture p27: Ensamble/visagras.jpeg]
  
</p>

- El regulador de 3V3 se tendia a sobre-calentar, por lo tanto fue necesario implementar un disipador de calor de aluminio sobre este componente, lo que posterior a las pruebas se pudo notar que su temperatura se disipaba perfectamente.

<p align="center">
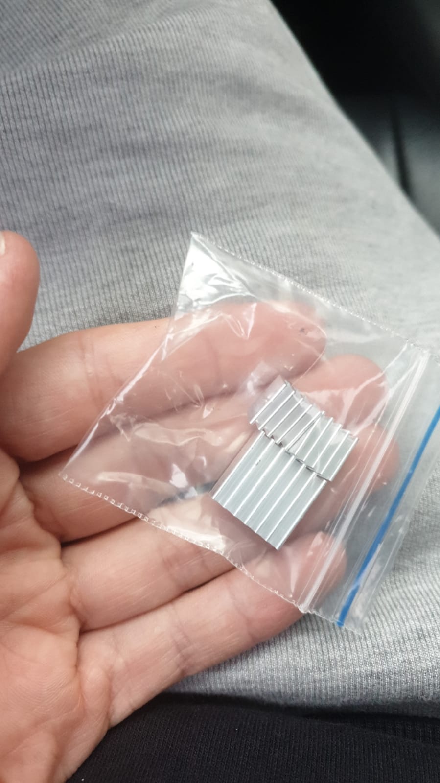
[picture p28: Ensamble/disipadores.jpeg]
  
</p>

- Luego nos dimos cuenta que no habia suficiente grosor para ajustar la tarjeta del proyecto con tornillos de sujeción a la base de la caja, por lo tanto se decidio  colocar 3 soportes de madera que impidieran que la tarjeta se moviera de su lugar.

<p align="center">
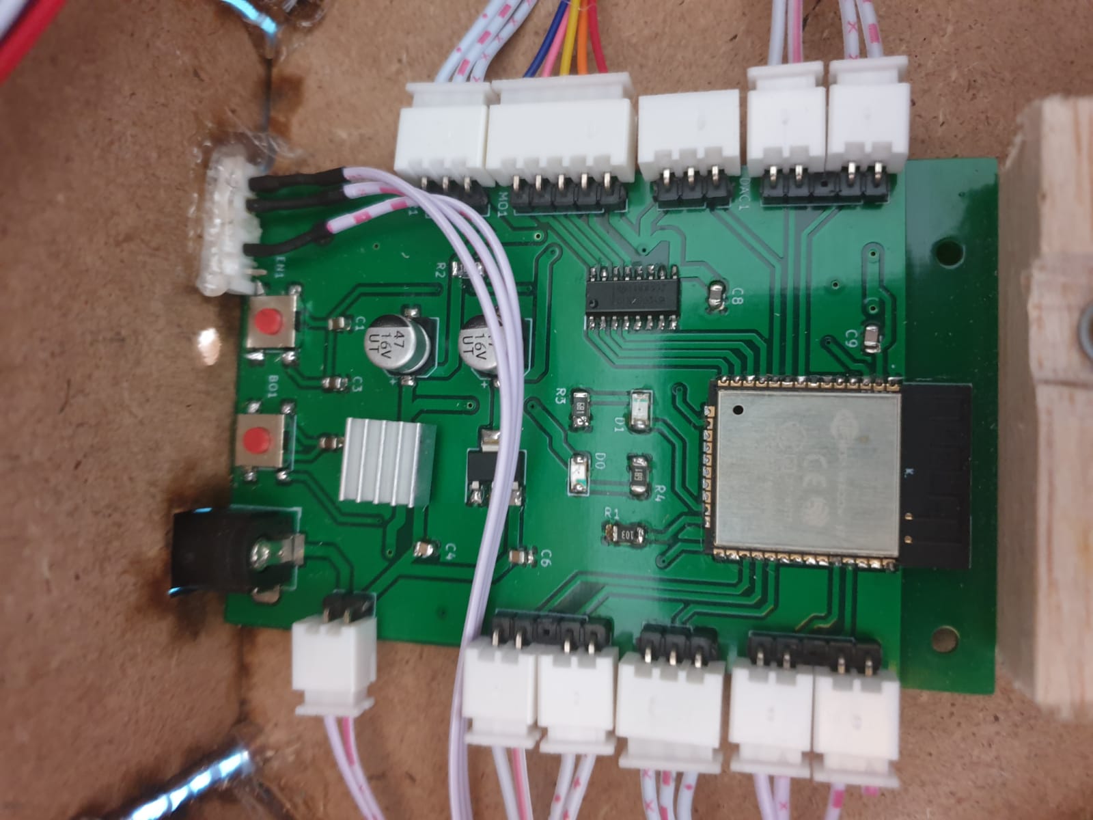
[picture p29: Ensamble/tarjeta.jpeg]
  
</p>

- Posteriormente se instalo el motor paso a paso, con dos soportes de madera que permitieron ajustarlo por medio de tornillos a la base de la caja.

<p align="center">
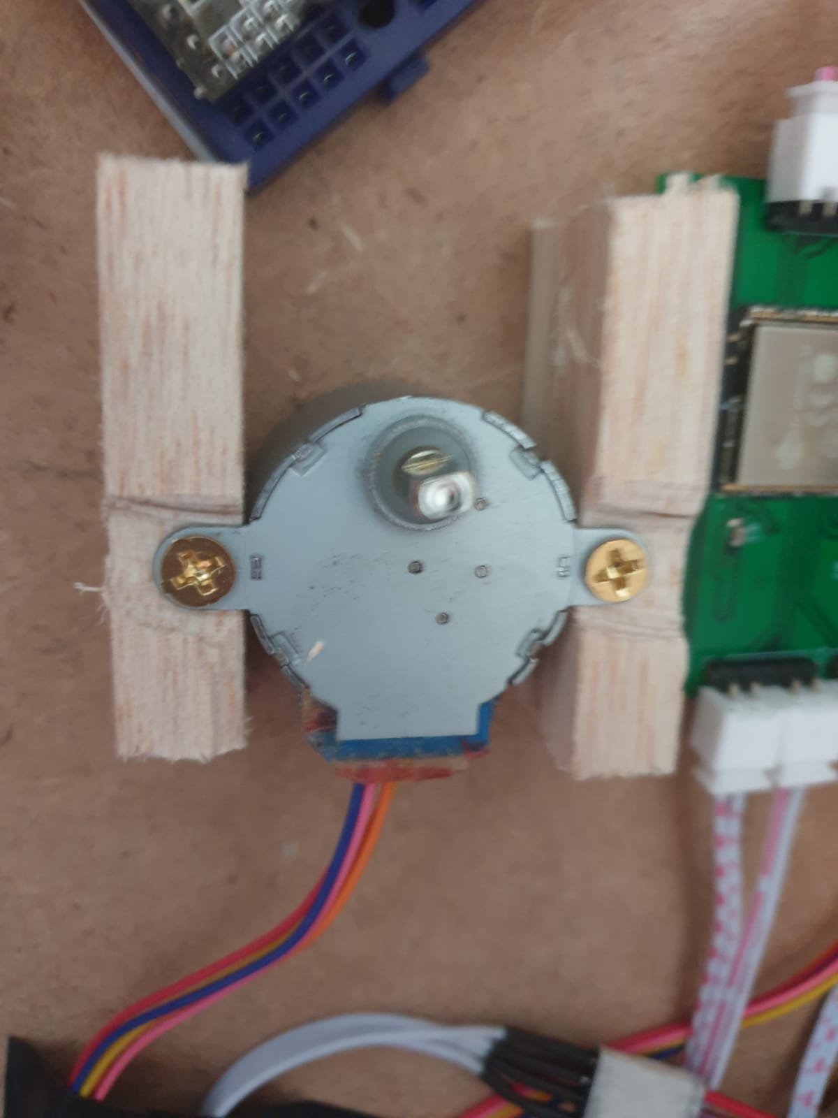
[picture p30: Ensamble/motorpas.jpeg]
  
</p>

- Con respecto al OLED y el infrarrojo, se instalaron en la tapa del dispositivo ya que facilita tanto su visibilidad como su funcionalidad.

<p align="center">
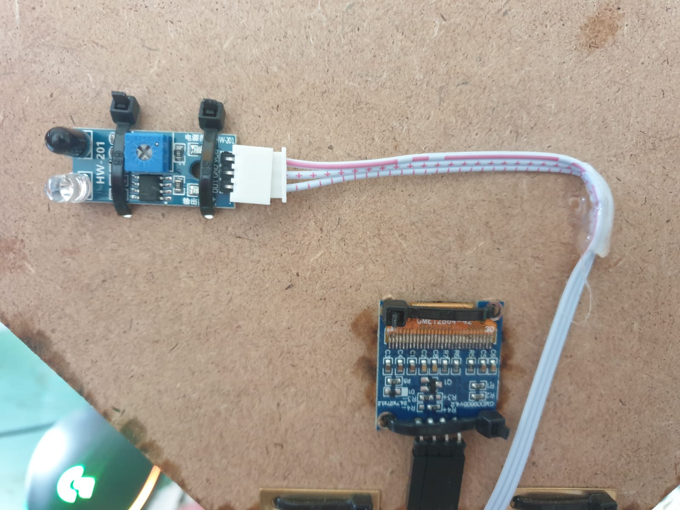
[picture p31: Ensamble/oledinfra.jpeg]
  
</p>

- El sensor PIR se instalo en la parte frontal del dispositivo ya que será el encargado de detectar el movimiento y si la mascota se acercó al dispositivo a comer.

<p align="center">
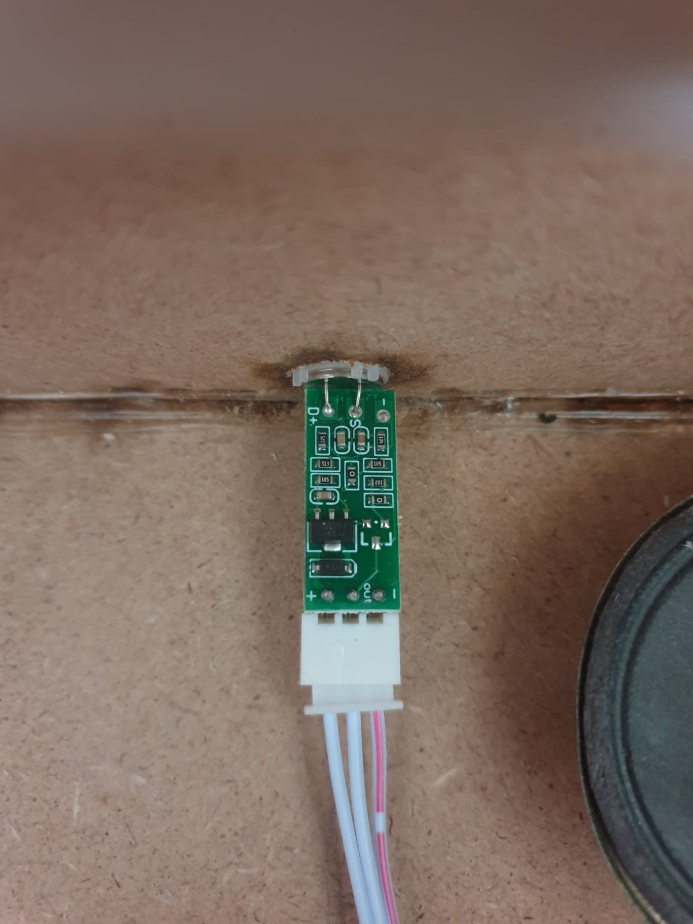
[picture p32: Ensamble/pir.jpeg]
  
</p>

- El reproductor de audio DFP y el parlante se ubicaron en la zona del motor, procurando que el parlante no se acercase a la tarjeta para no inducirr interferencia.

<p align="center">
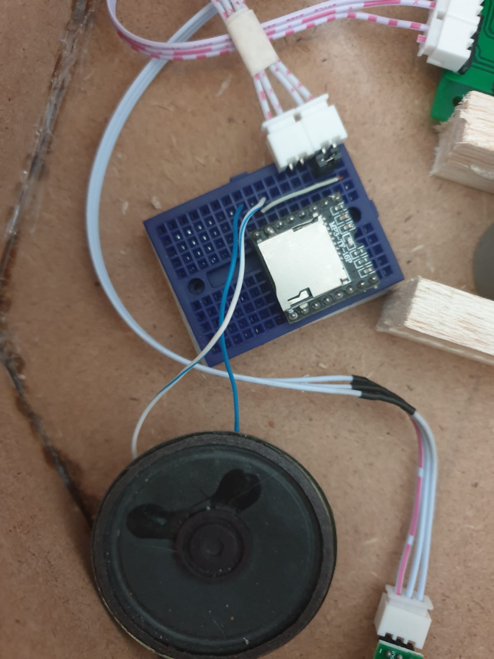
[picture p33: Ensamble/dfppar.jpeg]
  
</p>

- Sobre el motor paso a paso se instaló un plato desechable con un base de madera para que se ajustara al rotor del motor y pudiera girar.

<p align="center">
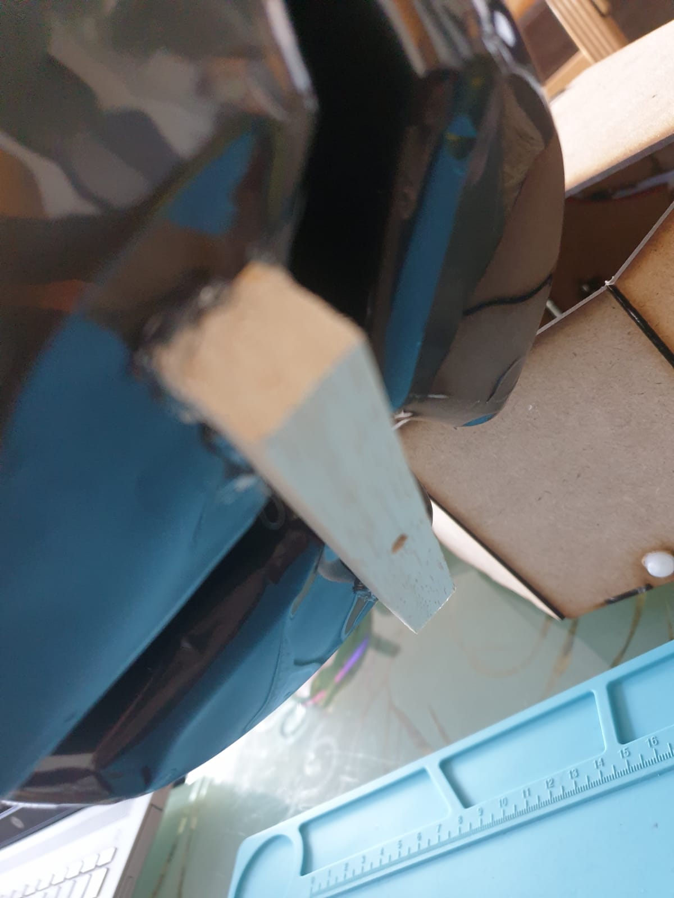
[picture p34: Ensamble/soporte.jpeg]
  
</p>

- Sobre una de las paredes de la caja se instalo un switch, para prender y apagar la tarjeta a voluntad.

<p align="center">
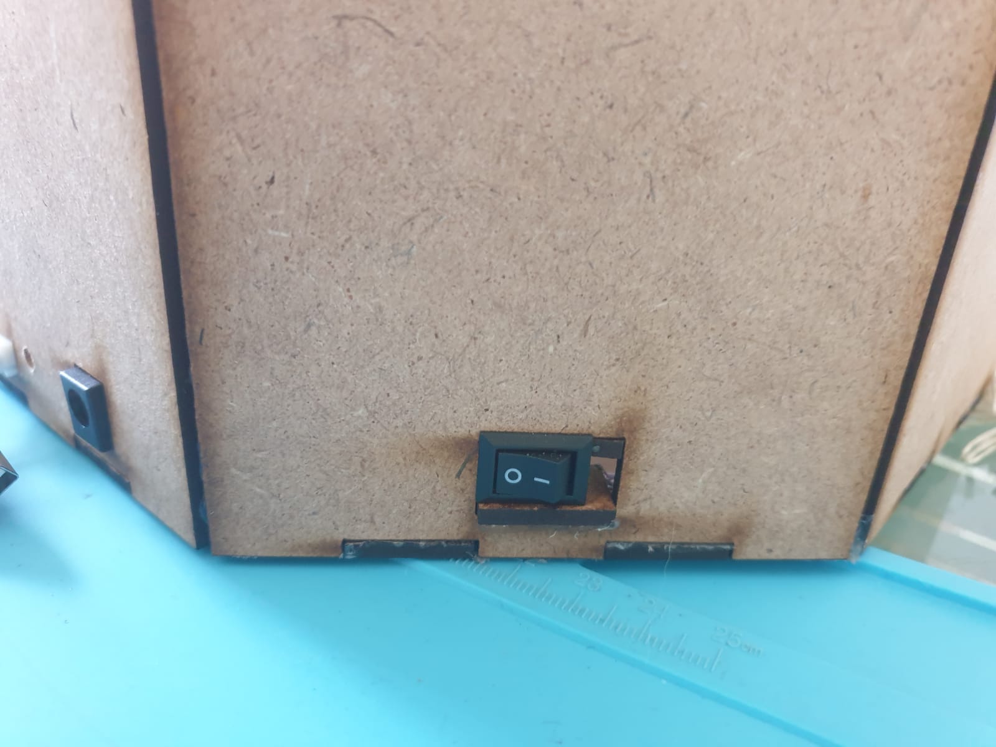
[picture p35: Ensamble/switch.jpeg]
  
</p>

- Sobre las paredes de la caja se pusieron soportes de madera para que el plato pudiese descansar sobre estos y mantuviera una posición horizontal a lo largo de su movimiento.

<p align="center">
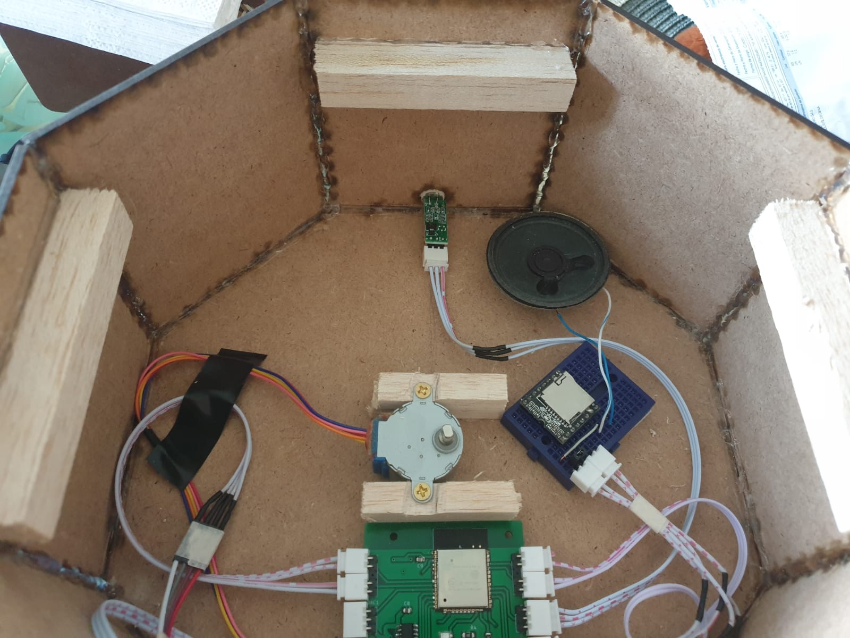
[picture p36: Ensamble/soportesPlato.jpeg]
  
</p>

### Resultado del montaje

<p align="center">
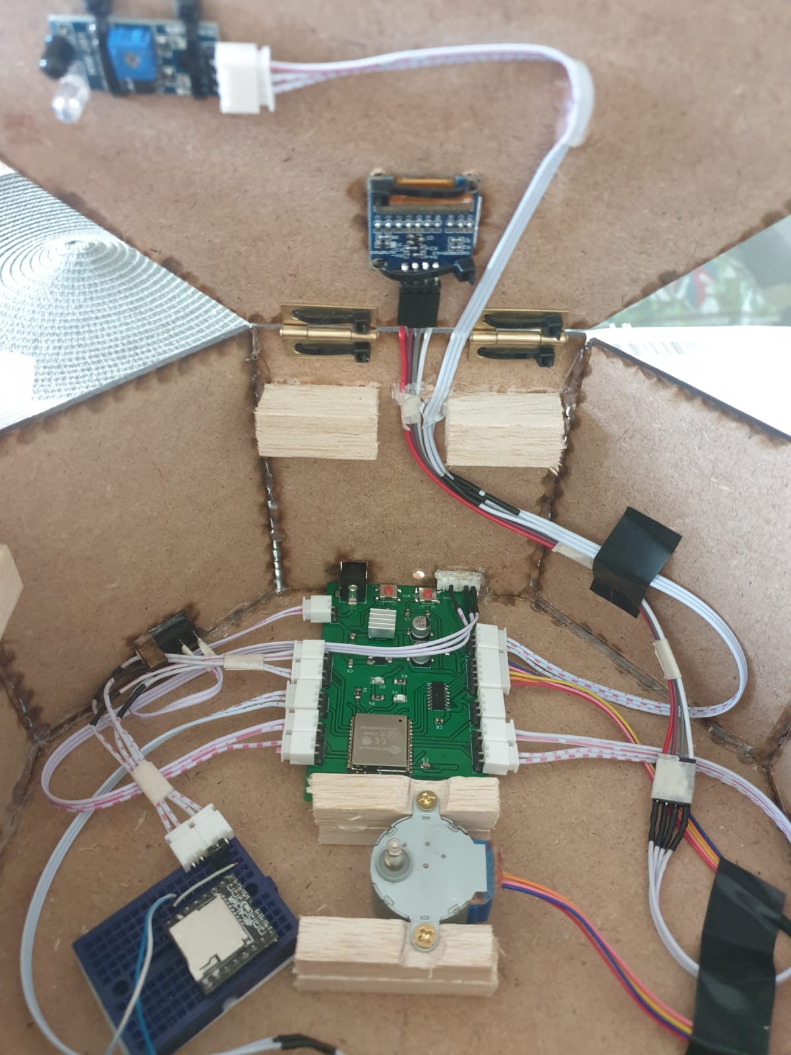
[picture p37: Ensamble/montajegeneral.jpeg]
  
</p>

## Firmware y Hardware

Como se explica en el repositorio, el metodo para subir cada una de las piezas de codigo al ESP32 se realiza por medio de comunicacion serial por su periferico UART0, por lo tanto para simplificar el proceso de programacion se decidio poner una salida para pines en una pared de la caja. De este modo no habia que retirar todo el montaje para hacer una simple conexion a UART.

<p align="center">
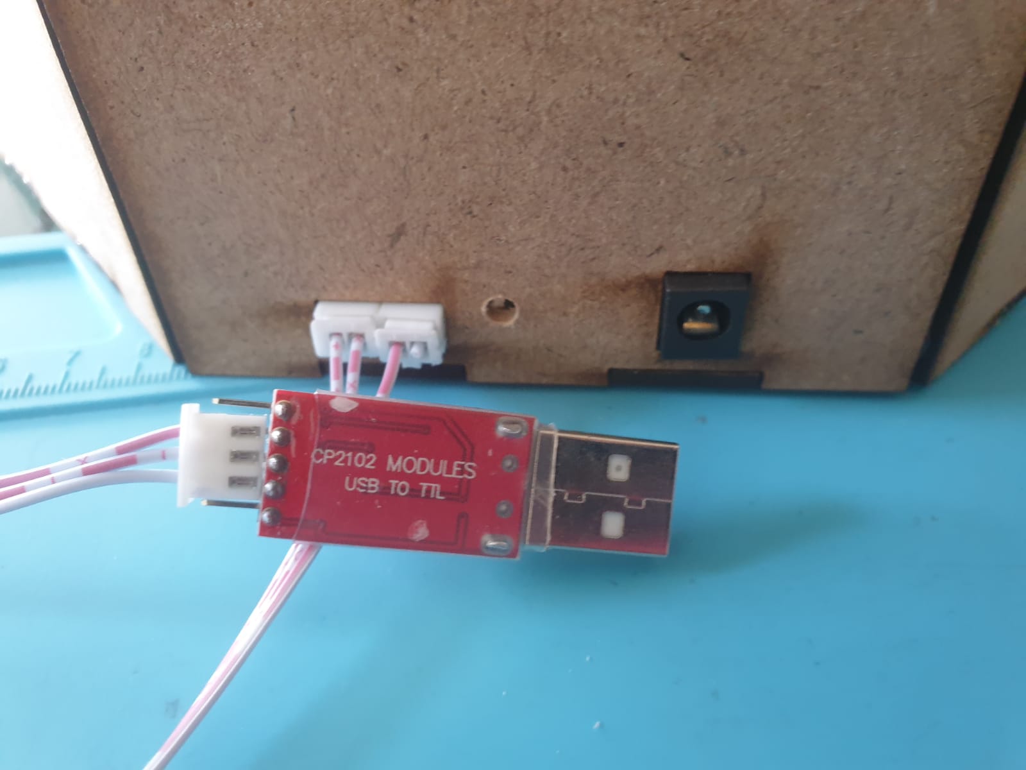
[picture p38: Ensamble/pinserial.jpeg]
  
</p>

## Conexión ESP32 y App

La conexión entre el ESP32 y la app movil en el dispositivo del usuario se realiza por medio de un broker MSQQ, donde ambos dispositivos se suscriben a topicos especificos y publican o reciben mensajes según el proceso que se desée realizar.

### Conexión APP

Para llevar a cabo la conexión de la APP con el brocker, inicialmente se descarga la librería **UrsPahoMQTTClient** en APPInventor y por medio de la programación en bloques dentro de la plataforma y un botón en el main de la App se realizá la conexión al brocker. 

<p align="center">
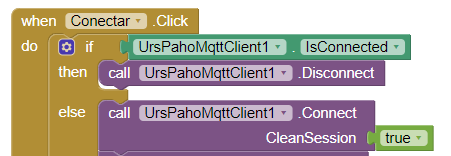
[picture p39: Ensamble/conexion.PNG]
  
</p>

De igual forma por medio de la programación de bloques, al momento que la App se conecta con el broker se publican en este el valor correspondiente del número de comidas establecidas por el usuario, la hora correspondiente a las comidas y el tipo de mascota, cada uno de estos valores en un topic independiente. A continucación se pueden observar unos ejemplo de la programación en bloques para realizar esta tarea:

<p align="center">
  
</p>

<p align="center">
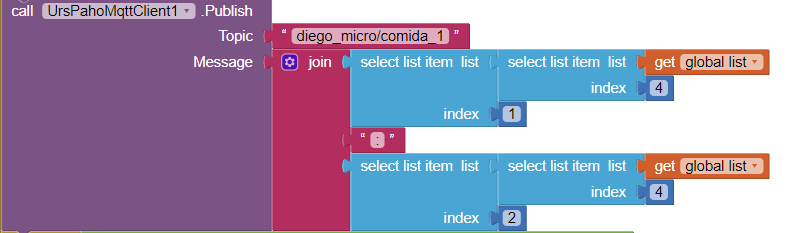
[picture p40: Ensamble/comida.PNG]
  
</p>

Luego, con el fin de obtener una variable que es publicada desde el ESP32 que corresponde al estado de la mascota, por medio de la programación en bloques se realizá la suscripción al topic *estado* y se iguala a una variable que se utilizara posteriormente en la APP para indicar el apetito de la mascota de manera gráfica.

<p align="center">
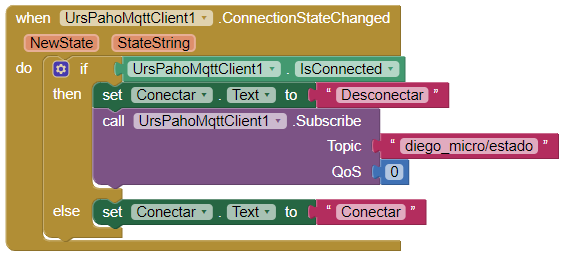
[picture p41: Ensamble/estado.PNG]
  
</p>

<p align="center">
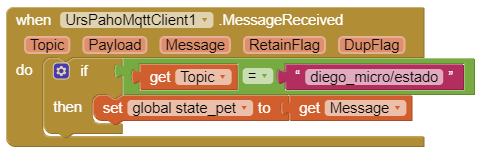
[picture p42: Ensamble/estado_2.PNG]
  
</p>

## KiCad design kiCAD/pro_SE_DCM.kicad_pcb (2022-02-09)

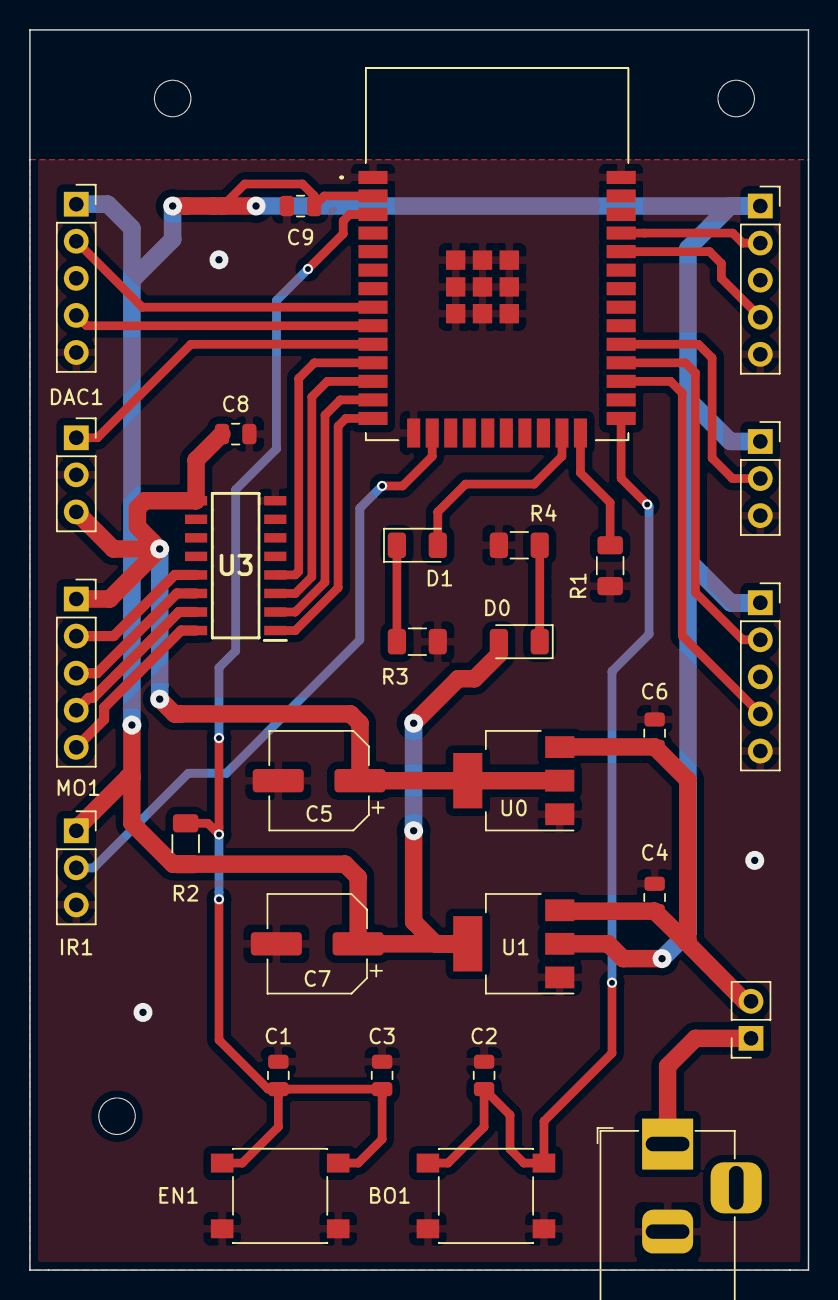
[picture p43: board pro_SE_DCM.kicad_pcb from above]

Board: 2 copper layers, 53.3 x 85.0 mm, 30 parts (0 on the bottom side), 28 nets.

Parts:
BO1: BTN_SMD; SW_Push_1P1T_NO_6x6mm_H9.5mm
C1: 1uF/16V(20%); C_0805_2012Metric
C2, C3, C8: 1uF/16V(10%); C_0805_2012Metric
C4: 10uF/16v; C_0805_2012Metric
C5, C7: 47uF/16V; CP_Elec_6.3x5.4
C6: 10uF/16V; C_0805_2012Metric
C9: 100pF/50v; C_0805_2012Metric
D0, D1: LED; LED_1206_3216Metric
DAC1: PARLANTE; PinSocket_1x03_P2.54mm_Vertical
EN1: BTN_SMD; SW_Push_1P1T_NO_6x6mm_H9.5mm
IR1: IR-FC51; PinSocket_1x03_P2.54mm_Vertical
J0: SW_ONOFF; PinSocket_1x02_P2.54mm_Vertical
J7: JACKDC; BarrelJack_Horizontal
MO1: M_28BYJ-48; PinSocket_1x05_P2.54mm_Vertical
OL1: OLED_BPP3N0; PinSocket_1x05_P2.54mm_Vertical
PIR1: HC-SR505; PinSocket_1x03_P2.54mm_Vertical
R1: 10K(1%1-1/4w); R_1206_3216Metric
R2: 10K(1%-1/4W); R_1206_3216Metric
R3, R4: 470(5%-1/8W); R_1206_3216Metric
U0: NCP1117-5.0_SOT223; SOT-223-3_TabPin2
U1: NCP1117-3.3_SOT223; SOT-223-3_TabPin2
U2: ESP32-WROOM-32_M103QH3200PH3Q0_; ESP32WROOM32M103QH3200PH3Q0
U3: ULN2003A; SOIC127P600X175-16N
UA1: UART_CP20102; PinSocket_1x05_P2.54mm_Vertical
UA2: DFPLAYER; PinSocket_1x05_P2.54mm_Vertical

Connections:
+3V3: C7.1, C9.1, D0.2, IR1.1, OL1.1, PIR1.1, R2.1, U1.2, U2.2, UA1.1, UA2.1
+5V: C5.1, C8.1, DAC1.3, MO1.1, U0.2, U3.9
/AD_INF: IR1.2, U2.16
/DAC0: DAC1.1, U2.10
/D_PIR: PIR1.2, U2.29
/EN: C1.1, C3.1, EN1.2, R2.2, U2.3
/IO0: BO1.2, C2.1, U2.25
/IO2: R1.1, U2.24
/PD_M0: U2.11, U3.4
/PD_M1: U2.12, U3.3
/PD_M2: U2.13, U3.2
/PD_M3: U2.14, U3.1
/RDX2: U2.27, UA2.4
/RXD0: U2.34, UA1.4
/SCL0: OL1.2, U2.8
/SDA0: OL1.4, U2.9
/TXD0: U2.35, UA1.2
/TXD2: U2.28, UA2.2
/USER: D1.2, U2.23
/m0: MO1.5, U3.16
/m1: MO1.4, U3.15
/m2: MO1.3, U3.14
/m3: MO1.2, U3.13
/reg_3.3/in: C4.1, C6.1, J0.2, U0.3, U1.3
GND: BO1.1, C1.2, C2.2, C3.2, C4.2, C5.2, C6.2, C7.2, C8.2, C9.2, DAC1.2, EN1.1, IR1.3, J7.2, OL1.5, PIR1.3, R1.2, R3.2, R4.2, U0.1, U1.1, U2.1, U2.15, U2.38, U2.39, U2.40, U2.41, U2.42, U2.43, U2.44, U2.45, U2.46, U2.47, U3.8, UA1.5, UA2.5
unnamed: D0.1, R4.1
unnamed: D1.1, R3.1
unnamed: J0.1, J7.1

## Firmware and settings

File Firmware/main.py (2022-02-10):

from machine import *
import time
import motor
import wlan
from umqtt.simple import MQTTClient
import ntptime
import OLED
import DFP
import gfx

# Global Variables

numComidas = 0
index = 0
comida1 = ("","")
comida2 = ("","")
comida3 = ("","")
tipo = 0
espera = 0
estadoMascota = [0,0]

#Pin_DEF
led = Pin(15,Pin.OUT) # Led de usuario
pir = Pin(5,Pin.IN) # Pin de PIR
infra = Pin(13,Pin.IN) # Pin de infra
scl = Pin(32,Pin.OUT, Pin.PULL_UP)
sda = Pin(33,Pin.OUT, Pin.PULL_UP)
pinesI2C = SoftI2C(scl = scl, sda=sda, freq = 400000)

#Motor_Config
motor.motorOff()
#Wifi_Config
wlan.do_connect()
#DFP_Config
DFP.DFP_setup()
#Oled_Config
oled = OLED.SSD1306_I2C(128, 64, pinesI2C, addr = 0x03C)
#GFX_Config
gfx = gfx.GFX(128, 64, oled.pixel)
oled.fill(0)
oled.show()

#Recv_info_fromBroker
def recv_info(topic, msg):
    global numComidas
    global comida1
    global comida2
    global comida3
    global tipo
    
    print(topic.decode())
    print(type(msg.decode()))
    if(msg == b'azul'):
        led.on()
        client.publish("diego_micro/example2", "Encendido")
    if(msg == b'rojo'):
        led.off()
        client.publish("diego_micro/example2", "Apagado")
    if(msg == b'motor'):
        motor.rotate(1000)
        client.publish("diego_micro/example2", "Moviendo")
    if(topic == b'diego_micro/numero_comidas'):
        numComidas = msg.decode()
        numComidas = int(msg)
        print(str(numComidas) + str(type(numComidas)))
    if(topic == b'diego_micro/comida_1'):
        com = msg.decode()
        comida1 = com.split(":")
        comida1[0] = int(comida1[0])
        comida1[1] = int(comida1[1])
        print(str(comida1[0]) + str(type(comida1[0])))
    if(topic == b'diego_micro/comida_2'):
        com = msg.decode()
        comida2 = com.split(":")
        comida2[0] = int(comida2[0])
        comida2[1] = int(comida2[1])
        print(str(comida2[0]) + str(type(comida2[0])))
    if(topic == b'diego_micro/comida_3'):
        com = msg.decode()
        comida3 = com.split(":")
        comida3[0] = int(comida3[0])
        comida3[1] = int(comida3[1])
        print(str(comida3[0]) + str(type(comida3[0])))
    if(topic == b'diego_micro/tipo'):
        tipo = msg.decode()
        tipo = int(tipo)

#Set_MQTTClient_toTopicSubscribe
client = MQTTClient('diego_micro/client1','broker.hivemq.com')
client.set_callback(recv_info)
client.connect()
client.subscribe(b"diego_micro/example1")
client.subscribe(b"diego_micro/numero_comidas")
client.subscribe(b"diego_micro/comida_1")
client.subscribe(b"diego_micro/comida_2")
client.subscribe(b"diego_micro/comida_3")
client.subscribe(b"diego_micro/tipo")

def rtcUpdate():
    timezone = -5
    a=1
    while(a):
        try:
            ntptime.settime()
            rtc = list(time.localtime())
            if((rtc[3]+timezone)<0):
                rtc[3] = rtc[3]+19
            else:
                rtc[3] = rtc[3]+timezone
            a=0
        except Exception as e:
            print(e)
            a=1
        time.sleep(3)
    return rtc

def stringHour(rtc):
    hour = str(rtc[3])
    if(rtc[4]<10):
        minute = "0"+str(rtc[4])
    else:
        minute = str(rtc[4])
    printHour = (hour,minute)
    return printHour

def proxCom():
    
    global numComidas
    global comida1
    global comida2
    global comida3
    
    com = [0,0,0,0,0,0]
    
    if((numComidas == 1) or (numComidas == 2) or (numComidas == 3)):
            com[0] = comida1[0]
            com[1] = comida1[1]
            com[2] = comida2[0]
            com[3] = comida2[1]
            com[4] = comida3[0]
            com[5] = comida3[1]
            
    return com

while True:
    
    # Bienvenida
    rtc = rtcUpdate()
    oled.fill(0)
    oled.text("BIENVENIDO",25,8)
    aux1 = stringHour(rtc)
    oled.text("Hora: "+ aux1[0] +":"+ aux1[1],22,25)
    oled.text("Proxima comida", 10,40)
    oled.show()
    client.check_msg()
    if(numComidas != 0):
        com = proxCom()
        oled.text("Hora: " + str(com[index])+":"+str(com[index+1]),22,50)
        oled.show()
        if(rtc[3] == com[index]):
            if(rtc[4] == com[index+1]):
                motor.rotate(170)
                if(tipo ==0):
                    DFP.sendInfo(0x16,0x00,0x00)
                    DFP.sendInfo(0x03,0x00,0x06) # Gatito
                if(tipo ==1):
                    DFP.sendInfo(0x16,0x00,0x00)
                    DFP.sendInfo(0x03,0x00,0x07) # Perrito
                v = pir.value()
                time.sleep(3)
                while((v==0) and (espera<10)):
                    v = pir.value()
                    espera = espera +1
                    time.sleep(1)
                if(espera>10):
                    estadoMascota[0] = 0
                else:
                    estadoMascota[0] = 1
                w = infra.value()
                if(w == 0):
                    estadoMascota[1] = 0
                else:
                    estadoMascota[1] = 1
                espera = 0
                index = index+2
                if((estadoMascota[0] ==0) and (estadoMascota[1] == 0)):
                    est = 1
                if((estadoMascota[0] ==0) and (estadoMascota[1] == 1)):
                    est = 4
                if((estadoMascota[0] ==1) and (estadoMascota[1] == 1)):
                    est = 8
                if((estadoMascota[0] ==1) and (estadoMascota[1] == 0)):
                    est = 4
                client.publish("diego_micro/estado", str(est))
                estadoMascota[0] = 0
                estadoMascota[1] = 0
                
        if(index > 4):
            index = 0
    
    time.sleep(1)
    
    

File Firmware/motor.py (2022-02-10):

from machine import Pin
import time


m0 = Pin(26,Pin.OUT)
m1 = Pin(27,Pin.OUT)
m2 = Pin(14,Pin.OUT)
m3 = Pin(12,Pin.OUT)

def motorOff():
    m0.off(), m1.off(), m2.off(), m3.off()


def rotate(flag):
   
    cont = 0
    s = 2
    x=0
    
    while (x<=flag):
        if(cont==0):
            m0.off(), m1.off(), m2.off(), m3.on()
            cont = cont+1
            time.sleep_ms(s)
        if(cont==1):
            m0.off(), m1.off(), m2.on(), m3.on()
            cont = cont+1
            time.sleep_ms(s)
        if(cont==2):
            m0.off(), m1.off(), m2.on(), m3.off()
            cont = cont+1
            time.sleep_ms(s)
        if(cont==3):
            m0.off(), m1.on(), m2.on(), m3.off()
            cont = cont+1
            time.sleep_ms(s)
        if(cont==4):
            m0.off(), m1.on(), m2.off(), m3.off()
            cont = cont+1
            time.sleep_ms(s)
        if(cont==5):
            m0.on(), m1.on(), m2.off(), m3.off()
            cont = cont+1
            time.sleep_ms(s)
        if(cont==6):
            m0.on(), m1.off(), m2.off(), m3.off()
            cont = cont+1
            time.sleep_ms(s)
        if(cont==7):
            m0.on(), m1.off(), m2.off(), m3.on()
            cont = 0
            time.sleep_ms(s)
        x = x+1
    x=0
    """
    while (x<=flag):
        if(cont==0):
            m0.on(), m1.off(), m2.off(), m3.on()
            cont = cont+1
            time.sleep_ms(s)
        if(cont==1):
            m0.off(), m1.off(), m2.on(), m3.on()
            cont = cont+1
            time.sleep_ms(s)
        if(cont==2):
            m0.off(), m1.on(), m2.on(), m3.off()
            cont = cont+1
            time.sleep_ms(s)
        if(cont==3):
            m0.on(), m1.on(), m2.off(), m3.off()
            cont = 0
            time.sleep_ms(s)
        x = x+1
    x=0
    """
    m0.off(), m1.off(), m2.off(), m3.off()

#rotate(170)
